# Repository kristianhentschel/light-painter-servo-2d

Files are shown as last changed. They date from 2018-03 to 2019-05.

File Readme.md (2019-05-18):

# 2D Lightpainting using Hobby Servos

A minimal lightpainting robot, using two servos driven by an Arduino mounted to
a 3D-printed scaffolding and moving an LED suspended by fishing line.

It can draw small shapes created in Inkscape using a GCODE format like a laser
cutter. Take a long exposure photograph in a dark room to reveal the drawing.

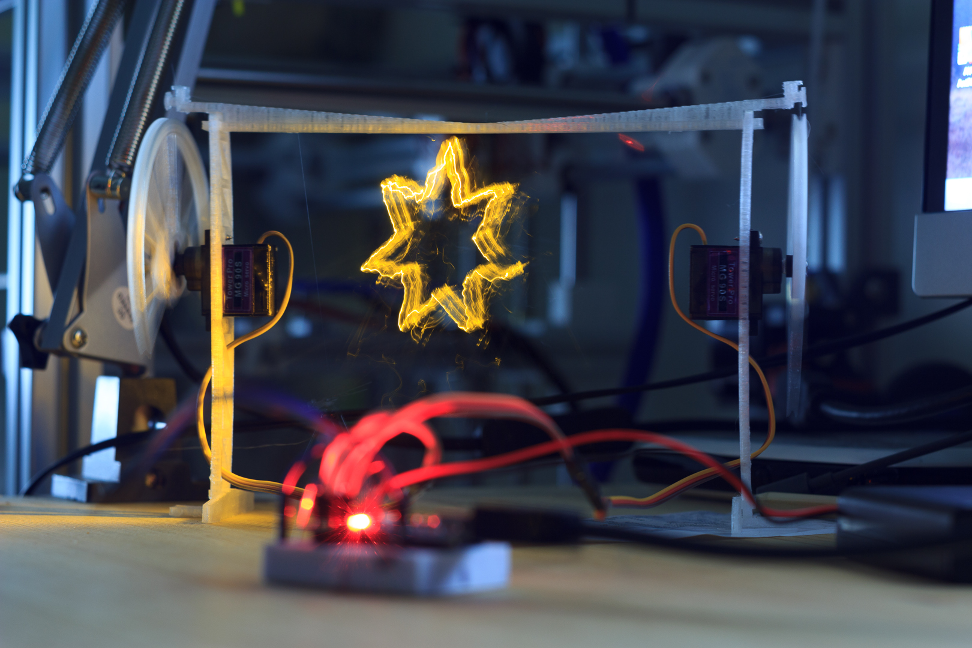
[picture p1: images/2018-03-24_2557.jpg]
a star painted by the finished robot


## Parts list and assembly

### Parts

  * Arduino nano or similar
  * A 5V power supply (3xAA batteries will do for 4.5V)
  * 2x `90S` micro servo (metal gear version preferred, e.g. `MG 90S`)
  * small breadboard and jumper wire
  * bright 3mm LED and appropriate resistor
  * fishing line (thin, flexible, strong, plastic thread)
  * thin wire to connect LED
  * small counterweight, such as a magnet or coin
  * Blue-Tack or similar to hold various things in place
  * 3D printed [parts](printed-parts/) (2x `gear`, 2x `foot`, 2x `stand`, 1x
    `beam`)

### Mechanical assembly

Clip the `foot` to the `stand`, and push in a servo so that the arm is outside,
as shown in the image above. Secure it with the top screw.

Repeat for the other side, then connect the two sides with the `beam`.

Fit a `gear` to each servo by removing the screw that holds the arm, clipping
the 3D printed part onto the arm, and securing it again with the screw.

You may need to take the arm off entirely to align it with the servo end
positions. The gear should be vertical at the end stops.

Cut two lengths of the fishing line to about 50cm. It can be shortened later!

Tie one end to the gear and secure with blue tack to ensure it goes into the
ridge when the gear turns.

Solder the thin wire to the LED and insulate with e.g. electrical tape.

Use Blue-Tack to hold together the LED and counterweight, and somehow connect it
to both fishing lines. When both sides are most extended, it should hover close
to the ground, horizontally centered in the frame.

_I haven't got a good solution for this part yet, I insulated the LED with
electrical tape, and sandwiched it with more Blue Tack and the fishing
lines between two small coins as counterweight._

### Electronics  

Make the connections on a breadboard using the jumper wires.

Servos:

* `brown` -> `GND` (if using a battery or external supplies, also connect its
  ground to the Arduino's `GND`)
* `red` -> `5V` (battery or external power supply recommended)
* `yellow` -> `D2` (left) and `D3` (right)

LED:

* `LED Anode` -> `D11`
* `LED Cathode` -> `GND`

Upload the [Arduino sketch](arduino/paint_2d/paint_2d.ino).

## Testing

Open a serial monitor (Arduino IDE) at `115200` baud. You should see a
`Hello World` message.

You can send GCODE commands on the serial connection, and this is also how the
more complex shapes will be drawn.

Write `M03` to turn the LED on, and `M05` to turn it off.

Try e.g. `G1 X20 Y20` to move to that position, and e.g. `G1 F600` to change the
feed rate (how fast the servos move).

## Drawing shapes

See [shapes/](shapes/star_0001.gcode) for an example SVG file and corresponding
GCode.

I used Inkscape to draw the shape (convert to path) and the JTech Photonics
Laser [plugin](https://jtechphotonics.com/?page_id=2012) to generate the GCODE.

Set the document unit to `mm` and the size to `120mm` width, `100mm` height.

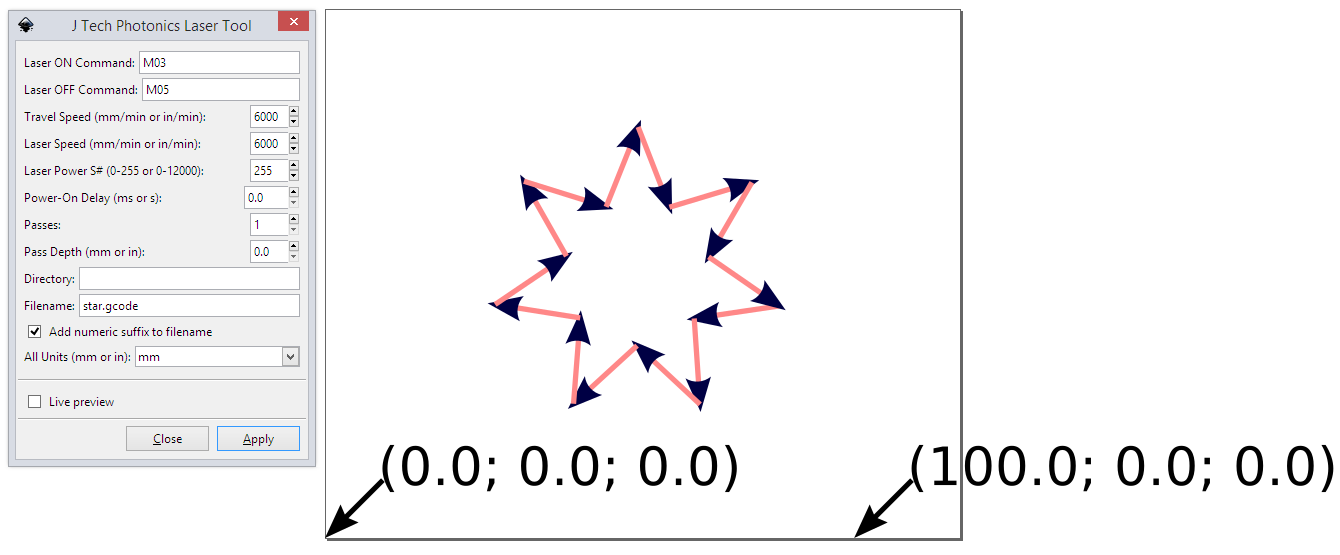
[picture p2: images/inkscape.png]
settings for laser plugin in inkscape


Copy and paste the generated GCODE into a serial terminal to draw the shape.

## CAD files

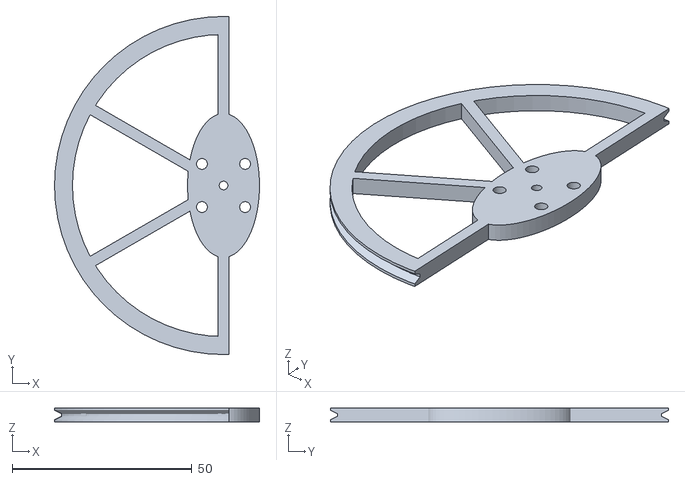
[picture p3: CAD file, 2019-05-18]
printed-parts/v1/gear.stl
57.0 x 94.0 x 4.00

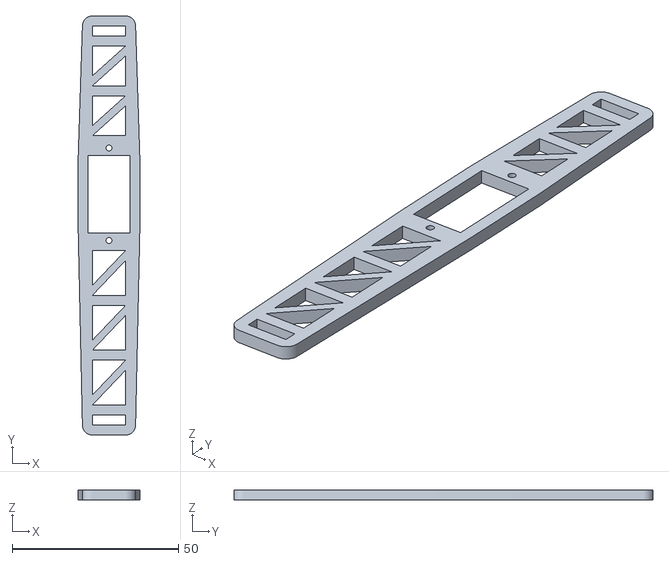
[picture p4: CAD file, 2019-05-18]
printed-parts/v1/stand.stl
18.5 x 126.0 x 3.00

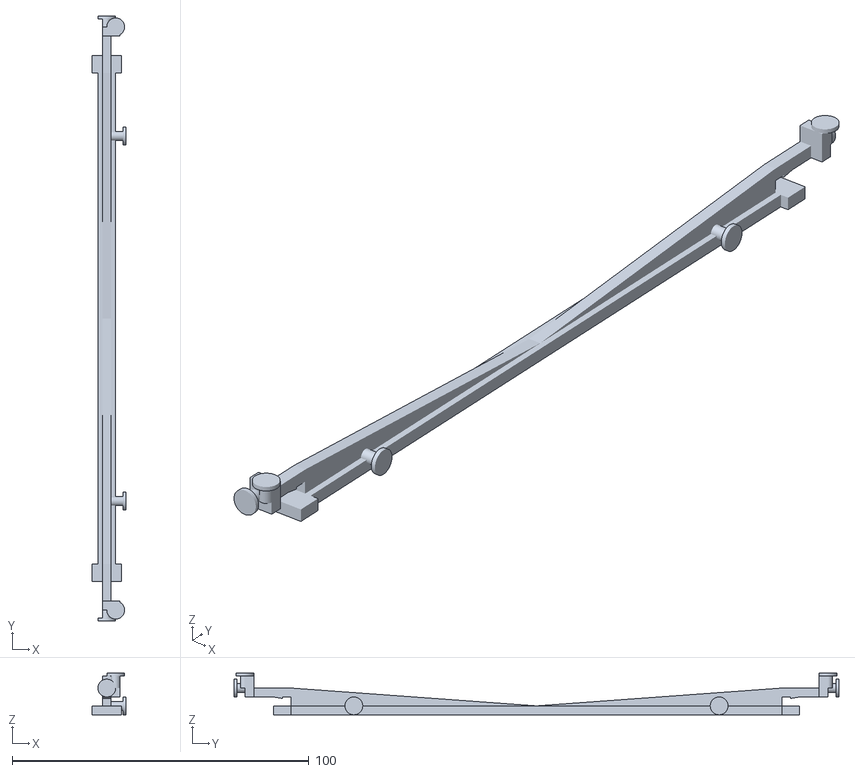
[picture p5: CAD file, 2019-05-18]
printed-parts/v1/beam.stl
11.5 x 203.7 x 14.0

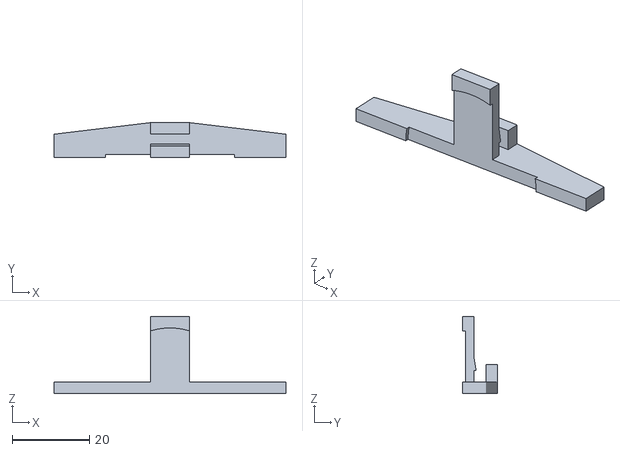
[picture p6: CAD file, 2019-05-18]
printed-parts/v1/foot.stl
60.0 x 9.00 x 20.0

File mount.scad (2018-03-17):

use <gear.scad>;

$fn = 100;

gear_diameter = 90;
body_length = 23.2;
body_width = 12.5;
body_height = 22.6;
mount_height = 2.8;
mount_offset = 21 - mount_height;
mount_length = 32.5;
gear_hood_diam = 12;
gear_hood_height = 5.7;
arm_spacing = 2.5;
mount_hole_diam = 1.75;
mount_hole_offset = (27.8 - body_length)/2;

module servo () {
  // origin is mounting point, center of gear attachment
  offset = [
    -(body_length - gear_hood_diam/2),
    -(body_width / 2),
    -(body_height + gear_hood_height + arm_spacing)
  ];

  translate(offset) {
    union() {
      cube([body_length, body_width, body_height]);
      translate([-(mount_length - body_length)/2, 0, mount_offset])
        cube([mount_length, body_width, mount_height]);
      translate([body_length - gear_hood_diam/2, body_width/2, body_height])
        cylinder(d=gear_hood_diam, h=gear_hood_height);
    }
  }
}

module example_gear_and_servo() {
  rotate([90, 0, 90]) {
    rotate([0, 0, 90])
      servo();
    gear();
  }
}

module servo_mount_cutout() {
  translate([-body_width/2, -(body_length - gear_hood_diam /2)]) {
    square([body_width, body_length]);
    translate([body_width/2, -mount_hole_offset])
      circle(d=mount_hole_diam);
    translate([body_width/2, body_length+mount_hole_offset])
      circle(d=mount_hole_diam);
  }
}

rim_width = 3;
stand_thickness = 3;
stand_height = 120;
stand_width = 10;

module triangle_cutouts(n=1, length = stand_width + rim_width) {
  l = length / 2 / n;
  for(i = [0:1:n-1]) {
    translate([-stand_width / 2, i * (l + 2 * rim_width)]) {
      polygon([
        [0, 0],
        [stand_width, 0],
        [stand_width, l]]);
      polygon([
        [0, rim_width],
        [stand_width, rim_width + l],
        [0, rim_width + l]]);
    }
  }
}

linear_extrude(height=stand_thickness){
  difference() {
    offset(r=rim_width) {
      hull() {
        servo_mount_cutout();
        translate([-stand_width/2, gear_diameter/2 - stand_height])
          square([stand_width, stand_height]);
      }
    }
    servo_mount_cutout();
    translate([-stand_width/2, gear_diameter/2 - rim_width])
      square([stand_width, stand_thickness]);
    translate([-stand_width/2, gear_diameter/2 - stand_height])
      square([stand_width, stand_thickness]);

    translate([0, gear_hood_diam]) {
      triangle_cutouts(n=2, length=gear_diameter / 2 - 2 * rim_width - stand_thickness);
    }

    translate([0, -(stand_height - gear_diameter / 2) + stand_thickness + rim_width]) {
      triangle_cutouts(n=3, length=stand_height - gear_diameter / 2 - 3 * rim_width - stand_thickness);
    }
  }
}

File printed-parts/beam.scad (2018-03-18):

include <common.scad>;
use <stand.scad>;

idler_diam = stand_rim_width;

module idler() {
  cylinder(d=idler_diam, h=gear_thickness);
  translate([0, 0, gear_thickness])
    cylinder(d=2*idler_diam, h=1);
}

gear_to_stand = gear_hood_height + arm_spacing + stand_thickness + (body_height - mount_offset);

module guide() {
  translate([0, -gear_to_stand, 2 * stand_rim_width]) {
    translate([-stand_thickness/2, 0, 0]) {
      cube([stand_thickness, gear_to_stand, 3]);
      translate([0, 0, 0])
        cube([idler_diam + stand_thickness, idler_diam, idler_diam + gear_thickness]);
    }
    translate([0, 0, idler_diam]) {
      translate([idler_diam, 0, 0])
        idler();
      translate([0, gear_thickness/3, 0])
        rotate([90, 0, 0])
          idler();
    }
  }
}

beam_length = stand_height + 2 * body_height;
beam_width = 6;
beam_support_height = 2 * stand_rim_width;

module half_beam() {
  translate([0, 0, gear_diam/2-stand_rim_width]) {
    // mounting point
    translate([-stand_width / 2, -stand_thickness * 2, 0])
      cube([stand_width, stand_thickness * 2, stand_thickness]);

    // base
    translate([-beam_width/2, 0, 0])
      cube([beam_width, beam_length/2, stand_thickness]);

    // vertical support and hook
    translate([-beam_width / 2 + stand_thickness / 2, 0, stand_thickness]){
      rotate([90, 0, 90])
        linear_extrude(height=stand_thickness)
          polygon([
            [0, 0],
            [0, stand_rim_width],
            [-stand_thickness, stand_rim_width],
            [-stand_thickness, stand_rim_width - 0.5],
            [-2 * stand_thickness, stand_rim_width],
            [-2 * stand_thickness, beam_support_height],
            [0, beam_support_height],
            [beam_length/2, 0]
          ]);
    }

    translate([stand_thickness/2, body_height - idler_diam/2, idler_diam])
      rotate([90, 0, 90])
        idler();

    guide();
  }
}

module beam() {
  half_beam();
  translate([0, beam_length, 0])
    mirror([0, 1, 0])
      half_beam();
}

beam();

// rotate([90, 0, 0]) {
//   stand();
//   translate([0, 0, -beam_length-stand_thickness])
//     stand();
// }

// difference() {
//   half_beam();
//   translate([-10, body_height, 0])
//   cube([20, 60, 100]);
// }

// translate([0, -gear_to_stand, 0])
// rotate([90, 0, 0])
// import("gear.stl");

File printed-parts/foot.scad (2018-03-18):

include <common.scad>;

foot_length = 3 * stand_width;
foot_length = gear_diam * 2/3;
foot_clip_height = 0.5;
foot_width = 2 * stand_width;

module foot() {
  difference() {
    union() {
      // foot
      linear_extrude(height = stand_thickness) {
        hull() {
          translate([-stand_width/2, stand_rim_width])
            square([stand_width, stand_thickness]);

          translate([-foot_length/2, -stand_thickness])
            square([foot_length, 2 * stand_thickness]);
        }
      }

      // hook
      linear_extrude(height = 2.5 * stand_thickness)
        translate([-stand_width/2, stand_rim_width])
          square([stand_width, stand_thickness]);

      // base
      linear_extrude(height = foot_width) {
        translate([-stand_width/2, -stand_thickness])
          square([stand_width, stand_thickness]);
      }

      // clip
      translate([-stand_width/2, 0, 2 * stand_thickness])
        rotate([90, 0, 90])
          linear_extrude(height = stand_width)
            polygon([
              [0, 0],
              [foot_clip_height, 0],
              [0, stand_thickness]
            ]);
    }

    // base cutout to get three point stand.
    translate([0, -stand_thickness, 0])
      rotate([-90, 0, 0])
        cylinder(d=foot_width * 2 - 2 * stand_thickness, h=stand_thickness/4);
  }
}

foot();

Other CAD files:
printed-parts/common.scad
printed-parts/gear.scad
printed-parts/lamp.scad
printed-parts/stand.scad

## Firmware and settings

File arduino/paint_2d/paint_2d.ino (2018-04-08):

#include <Servo.h>
#include "painter.h"
#include "settings.h"

// Global variables for the servo objects
Servo servo_left;
Servo servo_right;

// Set up the painter object, with function pointers to hide the Servo object.
void write_left(float value) {
  servo_left.write(value);
}

void write_right(float value) {
  servo_right.write(value);
}

void write_led(int value) {
  #if LED_USE_ANALOG_WRITE
  analogWrite(PIN_LED, value);
  #else
  digitalWrite(PIN_LED, value > 0);
  #endif
}

Painter painter(write_left, write_right, write_led);

// setup() creates the servo objects, enables the LED pin, and opens a Serial port.

void setup() {
  servo_left.attach(PIN_SERVO_LEFT);
  servo_right.attach(PIN_SERVO_RIGHT);

  pinMode(PIN_LED, OUTPUT);
  digitalWrite(PIN_LED, HIGH);

  Serial.begin(115200);
  Serial.println("Hello World.");
}

// loop() calls tick() once every TICK_MILLISECONDS.
// For initial testing, it also handles user input of movement commands.

unsigned long last_tick = 0;
void loop() {
  unsigned long now = millis();
  if (now - last_tick >= TICK_MILLISECONDS) {
    painter.tick();
    last_tick = now;
  }

  while (Serial.available() > 0 && painter.acceptInput()) {
    painter.input(Serial.read());
  }
}

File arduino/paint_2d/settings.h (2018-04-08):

#ifndef __SETTINGS_H__
#define __SETTINGS_H__

// ## Debugging
//
// Comment out to disable diagnostic prints to the Serial port.

#define DEBUG

// ## Pins

#define PIN_LED 11
#define PIN_SERVO_LEFT 2
#define PIN_SERVO_RIGHT 3

// ## Movement
//
// * The MAX_FEEDRATE limites the target movement speed, in mm per second. This
//   is also the default, if not set using the F parameter in the program.
// * The TICK_MILLISECONDS is the duration of a tick in ms. It effectively
//   controls the interpolation distance between positions.
// * The GEAR_RADIUS is a proxy for the circumference of the gear, controlling
//   the amount of movement a 180 degree rotation can give.
//
// The machine should be set up with both gears in the zero position, fully
// coiled up. The target should then be in a central position, at the top of the
// stage.

#define MAX_FEEDRATE 10000
#define TICK_MILLISECONDS 1
#define GEAR_RADIUS 45

// # LED
#define LED_USE_ANALOG_WRITE 0

// ## Stage Layout
//
// * The origin is at the bottom left.
// * The STAGE_WIDTH is the distance between the two idlers at the top.
// * The STAGE_OFFSET_TOP is the height of the area between the top of the
//   idlers, and the top of the stage, that is be used.
// * The STAGE_HEIGHT is the height of the active stage area only.
//
// Therefore, x values range from 0 to STAGE_WIDTH, and y values from 0 to
// STAGE_HEIGHT.
//
// The diagram below illustrates this:
//
// ```
//    y
//    ^
// ---O----------------O---
// SOT|\              /|
// ---|-\-----------/--|---
// ^  |  \        /    |
// SH | <---- SW ----> |
// v  |    \ /         |
// ---0-----*------------> x
//    ^(0, 0)
// ```

#define STAGE_WIDTH 120
#define STAGE_HEIGHT 100
#define STAGE_OFFSET_TOP 10

#endif // __SETTINGS_H__

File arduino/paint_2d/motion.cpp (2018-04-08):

#include <Arduino.h>
#include "motion.h"
#include "debug.h"

#define MIN(a, b) ((a) < (b) ? (a) : (b))
#define MAX(a, b) ((a) > (b) ? (a) : (b))

// #define PRINT_EVERY_TICK

Motion::Motion(int max_feedrate, int tick_duration, int gear_radius, int stage_width, int stage_height, int stage_offset_top){
  _max_feedrate = max_feedrate;
  _reposition_feedrate = _max_feedrate;
  _move_feedrate = _max_feedrate;
  _tick_duration = tick_duration;
  _gear_radius = gear_radius;
  _stage_width = stage_width;
  _stage_height = stage_height;
  _stage_offset_top = stage_offset_top;

  _pull_length = PI * _gear_radius;


  _current_x = 0;
  _current_y = 0;

  _interpolated_x = 0;
  _interpolated_y = 0;

  _target_x = 0;
  _target_y = 0;

  _dwell_ticks = 0;
  _idle = true;
  _spindle = 0;

  _move_total_ticks = 0;
  _move_current_tick = 0;
}

// returns true: if the command can be immediately executed, false if it needs
// interpolation.
#define IMMEDIATE true
#define INTERPOLATED false

bool Motion::plan(gcodeCommand command) {
  _command = command;

  // Acknowledge receipt of command
  Serial.print("ok ");
  Serial.println(command.N);

  switch(command.code) {
    case G0:
      DEBUG_PRINTLN("MOTION: G0");
      // Fast linear reposition.
      // X, Y: End position.
      // F: set repositioning feedrate.

      if (command.hasF && command.F > 0)
        _reposition_feedrate = _convert_feedrate(command.F);

      _feedrate = _reposition_feedrate;
      _start_move(command.hasX ? command.X : _current_x, command.hasY ? command.Y : _current_y);
      return INTERPOLATED;
      break;
    case G1:
      DEBUG_PRINTLN("MOTION: G1");
      // Linear move.
      // X, Y: End position.
      // F: set move feedrate.
      if (command.hasF && command.F > 0)
        _move_feedrate = _convert_feedrate(command.F);

      _feedrate = _move_feedrate;
      _start_move(command.hasX ? command.X : _current_x, command.hasY ? command.Y : _current_y);
      return INTERPOLATED;
      break;
    case G2:
      DEBUG_PRINTLN("MOTION: G2");
      // Circular move clockwise
      // move linearly with current feedrate as not implemented
      DEBUG_PRINTLN("MOTION: G2 not supported, moving linearly.");
      _feedrate = _move_feedrate;
      _start_move(command.hasX ? command.X : _current_x, command.hasY ? command.Y : _current_y);
      return INTERPOLATED;
      break;
    case G3:
      DEBUG_PRINTLN("MOTION: G3");
      // Circular move counter-clockwise
      // move linearly with current feedrate as not implemented
      DEBUG_PRINTLN("MOTION: G3 not supported, moving linearly.");
      _feedrate = _move_feedrate;
      _start_move(command.hasX ? command.X : _current_x, command.hasY ? command.Y : _current_y);
      return INTERPOLATED;
      break;
    case G4:
      DEBUG_PRINTLN("MOTION: G4");
      _start_dwell(command.hasP ? command.P : 0);
      return INTERPOLATED;
      break;
    case G21:
      DEBUG_PRINTLN("MOTION: G21");
      DEBUG_PRINTLN("MOTION: G21 units in mm, no action taken.");
      return IMMEDIATE;
      break;
    case G90:
      DEBUG_PRINTLN("MOTION: G90");
      DEBUG_PRINTLN("MOTION: G90 absolute positioning, no action taken.");
      return IMMEDIATE;
      break;
    case M03:
      DEBUG_PRINTLN("MOTION: M03");
      DEBUG_PRINTLN("MOTION: Spindle on.");
      _spindle = (command.hasS ? command.S : 255);
      return INTERPOLATED;
      break;
    case M05:
      DEBUG_PRINTLN("MOTION: M05");
      DEBUG_PRINTLN("MOTION: Spindle off. ignoring S if present.");
      _spindle = 0;
      return INTERPOLATED;
      break;
    default:
      DEBUG_PRINTLN("MOTION: Unknown gcode command.");
      return IMMEDIATE;
  }
}

// Convert a given feedrate from mm per minute to mm per second
float Motion::_convert_feedrate(float mm_per_minute) {
  return MAX(0, MIN(mm_per_minute / 60, _max_feedrate));
}

// start a move action.
//
// calculate how long it should take at current feed rate.
// reset the tick counter
//
void Motion::_start_move(float x, float y) {
  _target_x = MIN(MAX(0, x), _stage_width);
  _target_y = MIN(MAX(0, y), _stage_height);

  // calculate the distance (mm) and duration (ms) of the move
  float distance = sqrt(pow(_target_x - _current_x, 2) + pow(_target_y - _current_y, 2));
  float duration = distance / _feedrate * 1000.0;

  // convert duration to number of ticks
  _move_current_tick = 0;
  _move_total_ticks = ceil(duration / _tick_duration);

  _idle = false;

  DEBUG_PRINT("MOTION: Starting move from ");
  DEBUG_PRINT(_current_x);
  DEBUG_PRINT(", ");
  DEBUG_PRINT(_current_y);
  DEBUG_PRINT(" to ");
  DEBUG_PRINT(_target_x);
  DEBUG_PRINT(", ");
  DEBUG_PRINT(_target_y);
  DEBUG_PRINT(", duration = ");
  DEBUG_PRINT(duration);
  DEBUG_PRINT("ms, ticks = ");
  DEBUG_PRINTLN(_move_total_ticks);
}

// start a dwell action.
//
// calculate the number of ticks to wait.
void Motion::_start_dwell(float seconds) {
  // tick duration is in milliseconds.
  _dwell_ticks = (seconds * 1000.0) / _tick_duration;

  _idle = false;

  DEBUG_PRINT("MOTION: Starting to dwell for ");
  DEBUG_PRINT(seconds);
  DEBUG_PRINTLN(" seconds.");
}

float Motion::_interpolate(float start, float end, float t, float duration) {
  return start + (end - start) * (t / duration);
}

// Tick the motion planning.
//
// Dwell, or advance the current interpolated target position.
void Motion::tick() {
  // _dwell_ticks is set by a G4 command, do nothing for a while.
  if (_dwell_ticks > 0) {
    _dwell_ticks--;

    if (_dwell_ticks == 0) {
      _idle = true;
    }

    #ifdef PRINT_EVERY_TICK
    DEBUG_PRINT("MOTION: Dwell ticks remaining: ");
    DEBUG_PRINTLN(_dwell_ticks);
    #endif

    return;
  }

  // If there is a current linearly interpolated move, continue it.
  // actual actuator signals are created on demand using current, target position and tick progress.
  if (_move_current_tick >= _move_total_ticks) {
    // complete the move if no more ticks are needed to achieve it.
    _current_x = _target_x;
    _current_y = _target_y;
    _move_total_ticks = 0;
    _move_current_tick = 0;

    _idle = true;
  } else {
    // move the interpolated position along for the current tick.
    _move_current_tick++;

    _interpolated_x = _interpolate(_current_x, _target_x, _move_current_tick, _move_total_ticks);
    _interpolated_y = _interpolate(_current_y, _target_y, _move_current_tick, _move_total_ticks);

    #ifdef PRINT_EVERY_TICK
    DEBUG_PRINT("MOTION: Move tick ");
    DEBUG_PRINT(_move_current_tick);
    DEBUG_PRINT(" x = ");
    DEBUG_PRINT(_interpolated_x);
    DEBUG_PRINT(", y = ");
    DEBUG_PRINTLN(_interpolated_y);
    #endif
  }
}

// Return true if the motion planner is ready to accept the next command.
bool Motion::idle() {
  return _idle;
}
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

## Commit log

2018-03-16 Initial commit. modelling servo arm mount.
    [gear.scad]
2018-03-17 First print of 90mm 'gear'
    [gear.scad]
2018-03-17 make servo arm mount a bit bigger
    [gear.scad]
2018-03-17 Make servo arm screw hole go all the way through
    [gear.scad]
2018-03-17 Gear spur redone using rotational extrusion.
    [gear.scad]
2018-03-17 Add kinematics geogebra simulation.
2018-03-17 Add flat part of servo mount, without string guidance.
    [mount.scad]
2018-03-17 move common definitions to include file.
    [common.scad, gear.scad, stand.scad]
2018-03-17 Add a simple foot
    [foot.scad]
2018-03-17 redo triangle cutouts to more accurately fill given length
    [stand.scad]
2018-03-17 first draft of a cross beam to hold thread guides.
    [beam.scad]
2018-03-17 different beam design
    [beam.scad]
2018-03-18 Adjusted positioning of idlers, second part-test print of beam
    [beam.scad]
2018-03-18 First full print of beam (commented out test parts)
    [beam.scad]
2018-03-18 Second print of foot, added t bar and base cutout for three-point mounting
    [foot.scad]
2018-03-18 Implement most of the motion planning (except actual actuator positioning...)
2018-03-18 Fix interpolation bug not using start as offset. Add motion per tick debug prints.
    [motion.cpp]
2018-03-24 Rewrite the parser with more nested if else switch spaghetti. Should've used yacc long ago. Now accepts components in any order (line number first) with optional spaces (before checksum).
2018-03-24 Add example star shape + gcode file generated with laser plugin for inkscape.
2018-03-24 Actually turn LED on and off for M03 and M05.
2018-04-08 Implement PWM control for LED output, and make using it a setting
2019-05-18 Add Readme, images, STL files.
    [beam.scad, beam.stl, common.scad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]
